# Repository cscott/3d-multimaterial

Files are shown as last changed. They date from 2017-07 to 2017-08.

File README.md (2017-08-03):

# Direct-drive multimaterial printing using Printrbot extruders

Thing tracker at
https://cscott.github.io/thing-tracker/#/thing/3367036c-9556-4aa5-b3d4-02ff7dc592d1

## Description

This repository contains a collection of parts used to implement
direct-drive multimaterial printing on a [Printrbot] Simple Metal.
It should be generalizable to other Printrbot models, and other
3d printers, but we generally use Printrbot extruder designs
and [Marlin]'s [Printrboard]/[Extrudrboard] support.  The basic
direct-drive multimaterial concept is due to [Brian Roe](http://roemotion.com)
([@MakerBrian](https://twitter.com/MakerBrian)).

The direct-drive design uses the standard extruder directly above the
hot end for precise no-lag filament control and compatibility with
flexible filaments.  It is wired up to the extruder output on the
[Printrboard] and controlled by Marlin as "Extruder 0".

We use a Printrbot [Gear Head Extruder] for direct drive, using the
fact that this extruder is self-loading: once filament is introduced
above the drive gears, the extruder will grab it and feed it through
without manual intervention.  (We're actually using the [beta version
of the gear head extruder](https://www.youmagine.com/designs/printrbot-gear-head-extruder) which used a printed housing.)

Above this direct-drive gear head extruder is a V-shaped merge adapter
which accepts 1-4 bowden tubes containing different filament
materials.  This is integrated with the housing of the gear head
extruder to place the merge as close to the extruder input as
possible.  This minimizes the distance that unsupported filament must
travel during filament changes, and thus (hopefully) prevents jams.

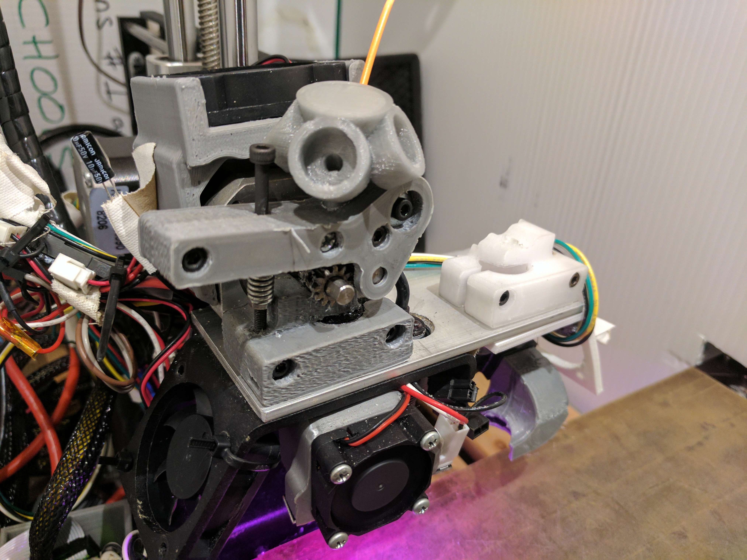
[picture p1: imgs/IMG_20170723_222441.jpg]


At the moment I've designed the merge as a single printed piece which
fits into an 8mm hole on direct-drive extruder handle or body.  The
idea is to make it easy to retrofit an existing gear-head extruder
by simply drilling an 8mm pocket in the handle, although I don't
own one of the newer Aluminum Gear Head Extruders to fully test this.

The bowden tubes from the merge piece run to individual bowden drives
mounted on filament spools.  I'm using SPANNERHANDS' excellent
[spool design](https://www.thingiverse.com/thing:2119644) with a
slight remix to move the PFTE coupler and mount an extruder where
the PFTE coupler used to attach.  The extruders connect to an
[Extrudrboard] or [Extrudrboard2] and feed the filament from the
spool into the bowden tube to direct it to the merge piece.
Two extruders are always driven simultaneously to move filament,
one on the spool and one at the print head, although during
filament change operations there may be times when no filament
is actually in contact with the direct drive, and thus the
spool extruders are working alone.

The [Marlin] firmware is modified to support this style of operation,
building on the `MK2_MULTIPLEXER` support upstreamed to support Prusa's
[Super Switch](https://github.com/prusa3d/Original-Prusa-i3/issues/29).

<br clear="both" />

## Instructions

### Step 1: Build spools

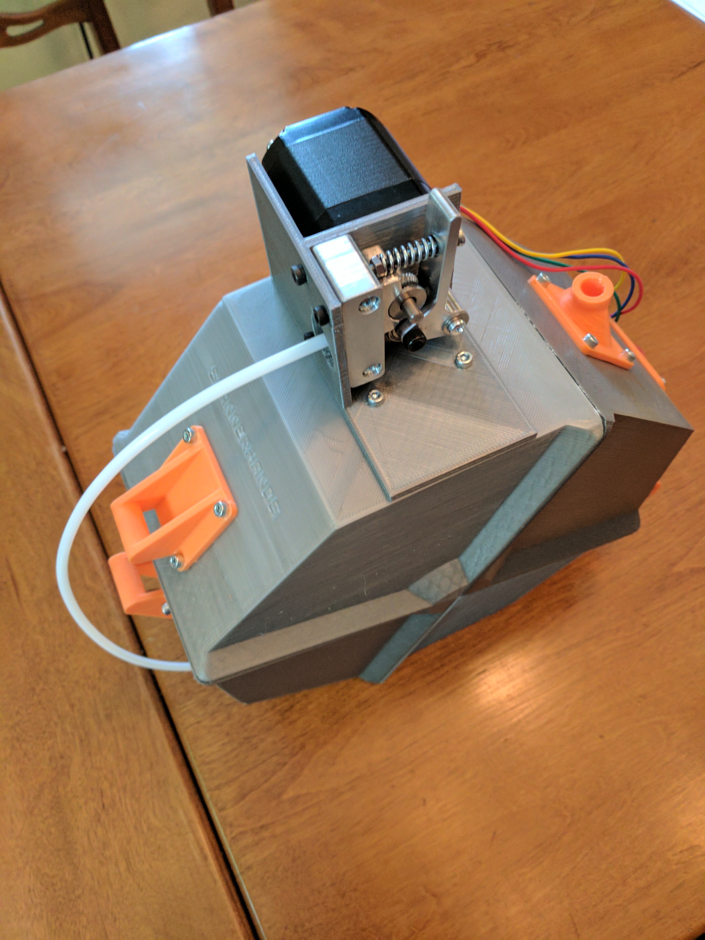
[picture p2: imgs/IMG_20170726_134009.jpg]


Start by printing out a [SPANNERHANDS spool] for each filament bowden
extruder you are going to use. I'm using the "v5 1kg" variant, but
with a little effort you could adapt these instructions to one of the
other spool variants.  Use [`spool-remix-lid2.stl`] instead of the
stock `LID2` part.  Mount the SPANNERHANDS `PTFE_COUPLER_v2_0.stl`
part to [`spool-remix-lid2.stl`].  We are going to mount our
bowden extruder on `LID1`, where the `PTFE_COUPLER` part would
normally go.  Assemble the `LID_Bracket`, `BASE_Bracket`,
and two `CLASP_BRACKET_v2_0` parts; I printed these in a contrasting
color.

Use two `Glue_Joint` parts to assemble the lid and base halves;
I recommend gluing both at once with the parts assembled into a complete
circle so you can ensure that the gap between top and bottom is not
too large as you glue them up.  Otherwise you tend to get top and bottom
halves which are ~178° of arc instead of 180°, and when you finally put
top and bottom together you get a pacman which won't close completely.
You can scale up the Z axis of the SPANNERHANDS `Flex_Seal` parts and
then trim them into a wedge to kludge around the problem if this happens.

I found the stock spool bearing mounts a little too tight, so I printed
the 50mm spool at 102% to fit my 52mm-core diameter spools with the right
fit for the bearings.  I use the remix at
[thing:2372633](https://www.thingiverse.com/thing:2372633) to fit my
32mm core diameter spools; I didn't need to scale that in any way.

<br clear="both" />

### Step 2: Mount bowden extruders

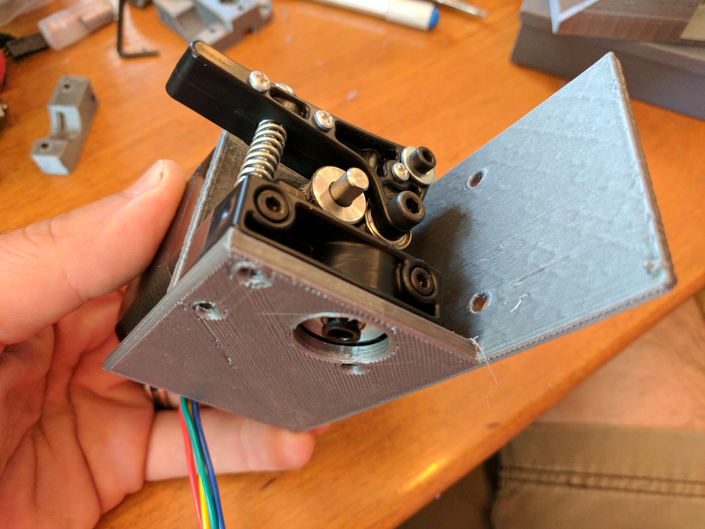
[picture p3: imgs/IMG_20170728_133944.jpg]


Now print out [`mount-1kg.stl`] and attach it to the LID1 part of the
spool, with four M3x10mm screws like all of the other SPANNERHANDS
spool parts.  After it is attached to the spool you can mount the
extruder, placing the mount between the extruder body and the stepper.
I recommend M3x25mm screws here; some models of Printrbot extruder
might need some extra length to account for the mounting plate between
the extruder and stepper.

You can optionally use three M3x8mm screws to secure the bottom of
the extruder.  Some models of Printrbot extruder (for example, the
injection-molded plastic extruder) don't have these mounting holes.
They are probably overkill for this use anyway.

<br clear="both" />
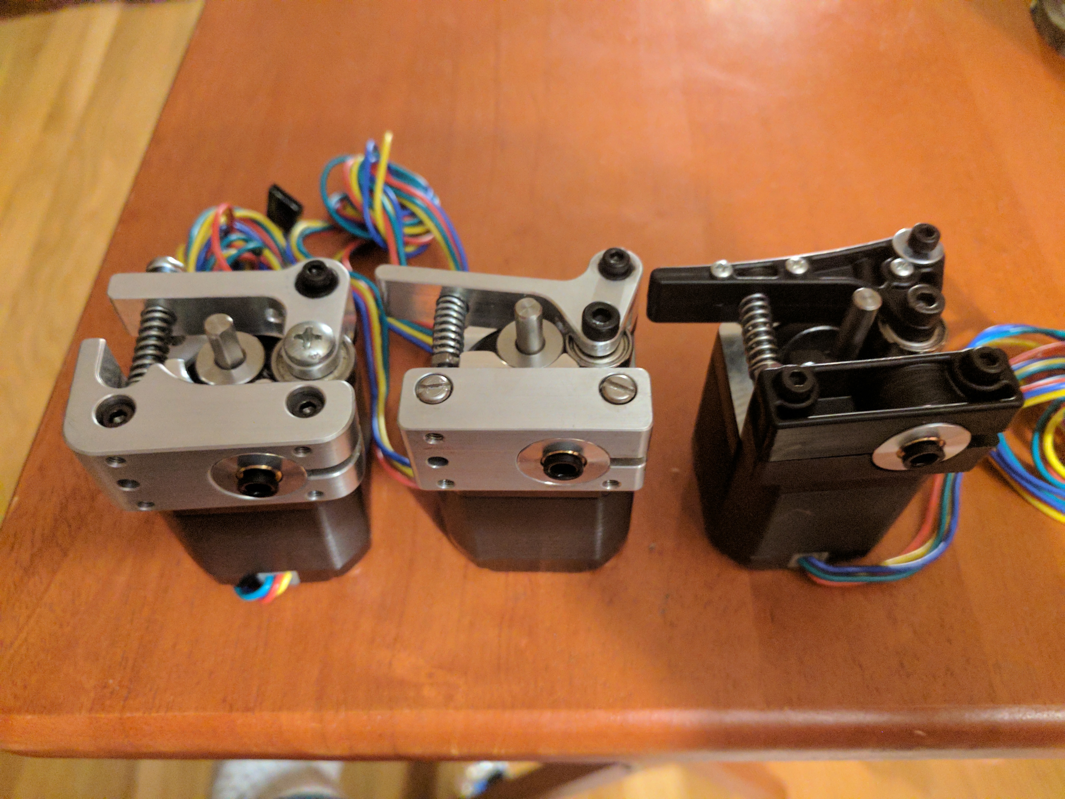
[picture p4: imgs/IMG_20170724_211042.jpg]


Insert a
[Groove mount 1.75mm Bowden coupler](https://www.filastruder.com/collections/e3d-spare-parts-and-accessories/products/bowden-couplings-all-types)
where the hotend would usually mount on the extruder.

<br clear="both" />
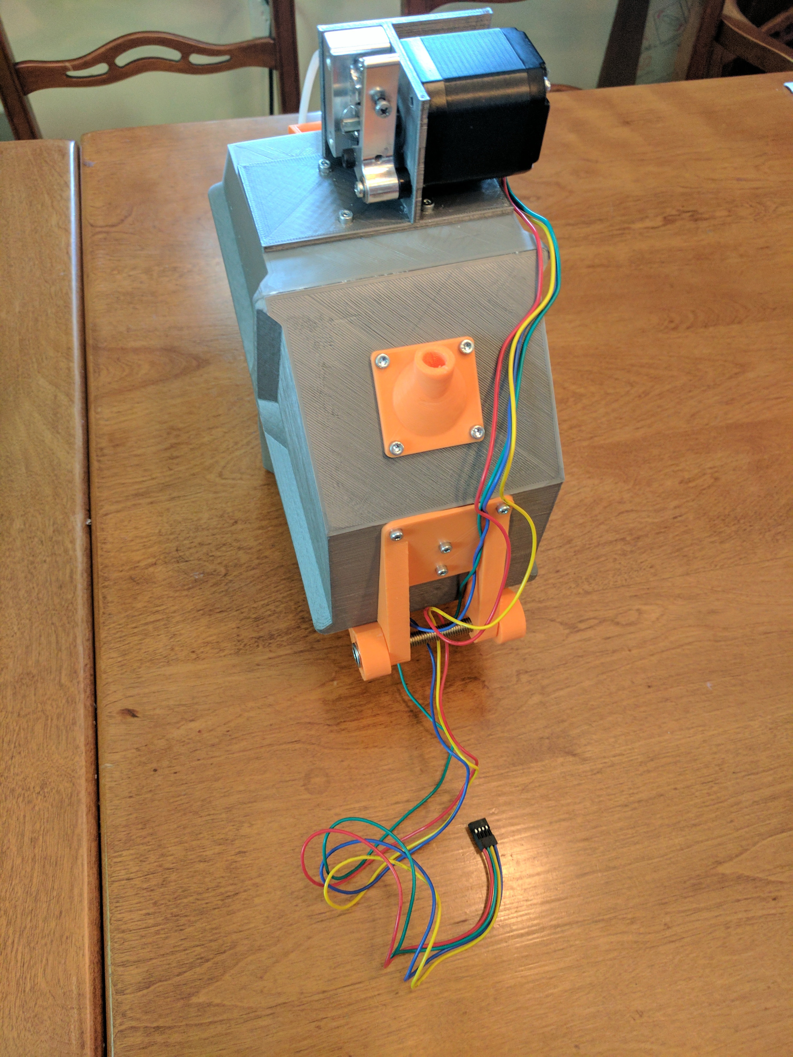
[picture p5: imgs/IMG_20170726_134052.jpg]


You can route the wires for the stepper down the back of the spool and
through the hinge.  You'll probably need [servo extension cables] to
reach your Extrudrboard/Extrudrboard2 from wherever you decide to
mount your spools.  You can use [`spool-remix-hanger.stl`] to mount
the spool to the wall while leaving room for the stepper motor cable.

<br clear="both" />

### Step 3: Assemble gear head direct-drive extruder

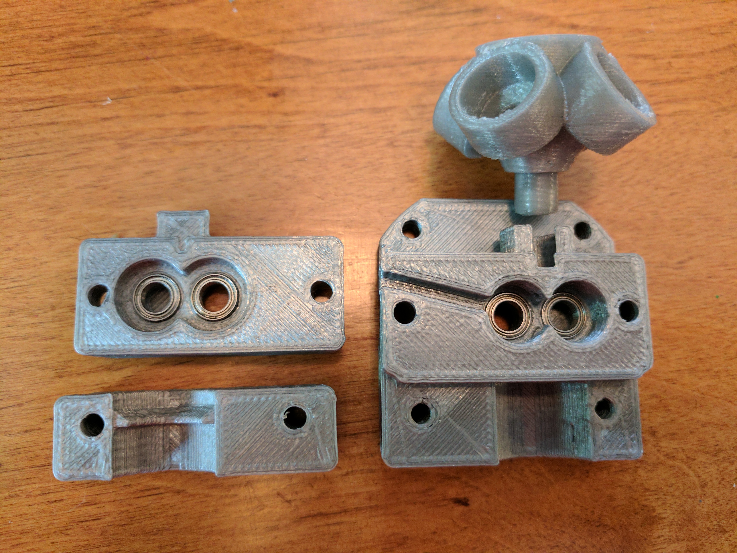
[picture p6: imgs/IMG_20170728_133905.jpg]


Print out [`gearhead-remix-base.stl`], [`gearhead-remix-clamp.stl`],
and [`gearhead-remix-gearbox.stl`]. (The photo also shows an early
version of [`bowden-block-4.stl`], the bowden merge piece.)

<br clear="both" />
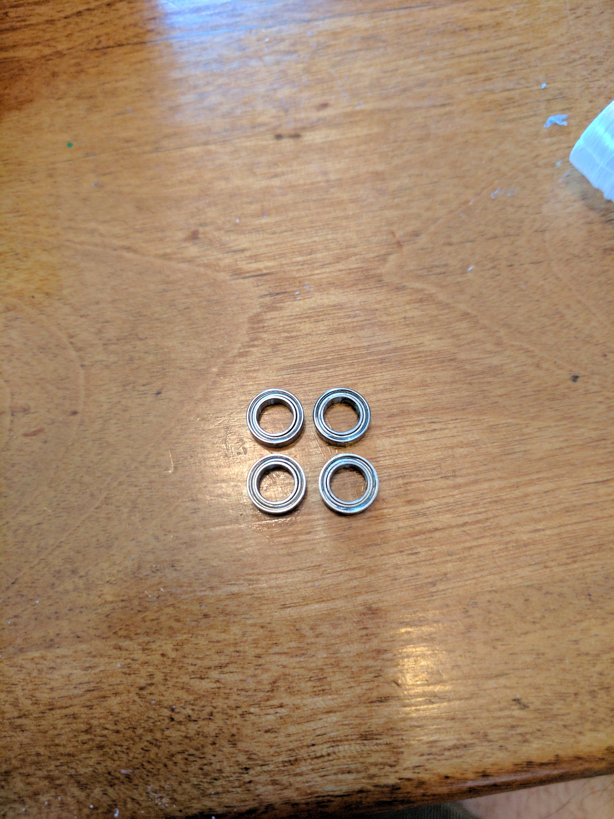
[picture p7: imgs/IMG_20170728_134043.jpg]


You'll also need (4) [5x8x2.5mm ball bearings] (or just three; see
note 2 below).

<br clear="both" />


First, install a pair of bearings into the `base` piece, and then install
the Printrbot Gear Head Extruder Gear Set into the bearings.

**NOTE 1:**
Printrbot [sells these](https://printrbot.com/shop/gear-head-extruder-gear-set/),
but the pair that I have came from the Beta program for the Gear Head Extruder.
It's possible the production gear set differs from the beta gears.

**NOTE 2:**
Printrbot's original instructions stated that the rear stepper motor
bearing (the bearing behind the hollow gear you just installed) is
optional.  But if you're buying bearings, no reason to pinch pennies.

**NOTE 3:**
You may want to try [walter](https://www.thingiverse.com/walter/about)'s
[remix of the gear head extruder](https://www.thingiverse.com/thing:1052966).
It appears to use the same Printrbot gear set and bearings---but again,
I'm not certain whether production gears differ from beta gears, and if so
which walter used.  Some modifications will be necessary to adapt his
remix to Printrbot bottom-mounting holes, but maybe you don't need those.

<br clear="both" />
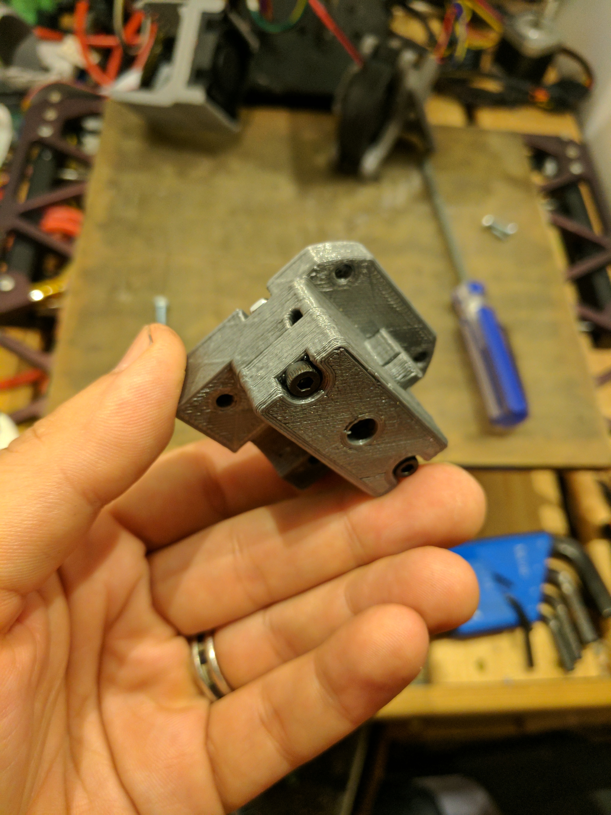
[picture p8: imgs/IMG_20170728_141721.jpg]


Now install the other pair of bearings into the `gearbox` piece, and
bolt it to the base using (2) M3x20mm screws and (2) M3 nuts, sandwiching
the gears between them.  Before closing things up, align the set screw in
the left-hand gear with the channel in the base; this will allow you to
insert an allen wrench to tighten this gear onto the stepper shaft.

<br clear="both" />
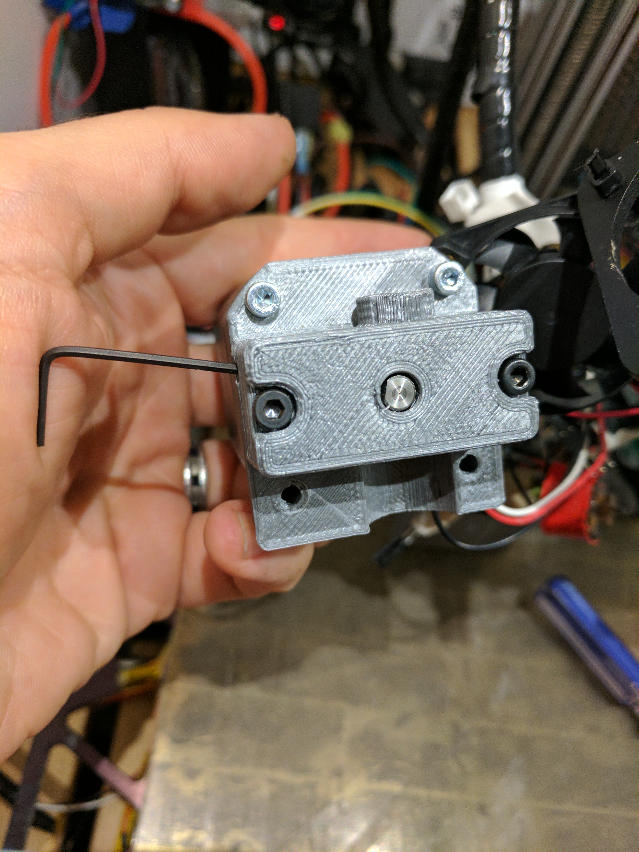
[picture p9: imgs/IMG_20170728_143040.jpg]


Attach the assembled gear box to the stepper.  Ensure the flat on the stepper
shaft is aligned with the allen wrench channel.  Use (2) M3x10mm screws in
the top holes to attach the gear box to the stepper, and then tighten the
set screw to secure the drive gear to the stepper shaft.

You probably want to use `M302 P1` to allow cold extrudes, then hook up
your stepper at this point and do a test extrusion w/o filament or hot end
in order to check that the gears turn smoothly without slipping or grinding.

<br clear="both" />
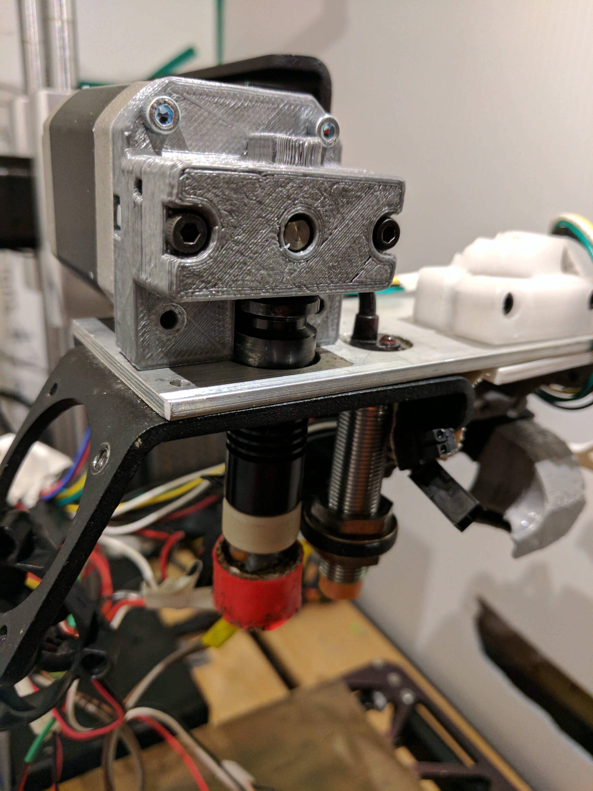
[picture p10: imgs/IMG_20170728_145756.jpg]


Now attach the extruder to the Y-axis of your printer using (2) M3x10mm
screws through the bottom mounting holes into (2) M3 nuts in the slots
provided.  (I'm using M3x12mm screws because I have an extra 3mm aluminum
plate mounted to my Y-axis, to support a previous dual-extruder
experiment [similar to this one](https://www.thingiverse.com/thing:1539380).)

Insert your hot end, and ensure it is snug and flush to the bottom surface
fof the extruder as shown in the picture.  Any gap here will allow flexible
coil to kink and coil into the gap, eventually pushing your hot end off in
the middle of a print.  (This is the voice of experience speaking.)

<br clear="both" />
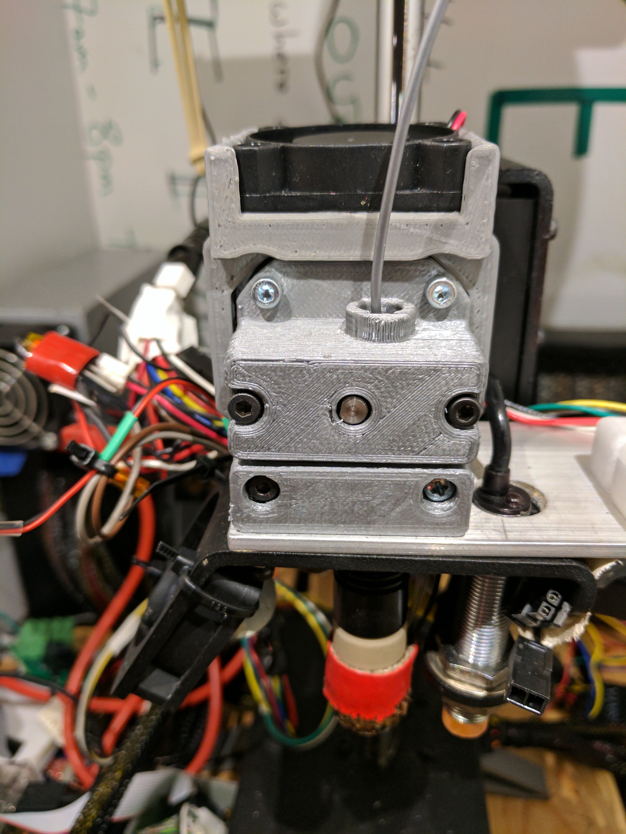
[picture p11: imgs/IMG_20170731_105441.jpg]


Install the `clamp` piece using two M3x22mm screws into the stepper.
There is a ridge on the clamp piece that should fit into the ring at
the top of your hot end and keep it from slipping downward.  Be
careful of the screw length here: if the screw is too long it will
bottom out in the blind mounting hole on the stepper and not bend the
PLA clamp piece enough to properly grip the hotend.  (Again, the voice
of experience.)  The `clamp` is secured to the Y-axis using another
M3x10mm screw and M3 nut into its bottom.

You can do a test print, feeding filament through the hole in
the top of the remixed gear head extruder, to make sure everything
is working correctly to this point.  Be sure to use `M92 E127` to
reset your extruder steps/mm if you weren't previously using a
gear head extruder.

<br clear="both" />

### Step 4: Install bowden merge piece

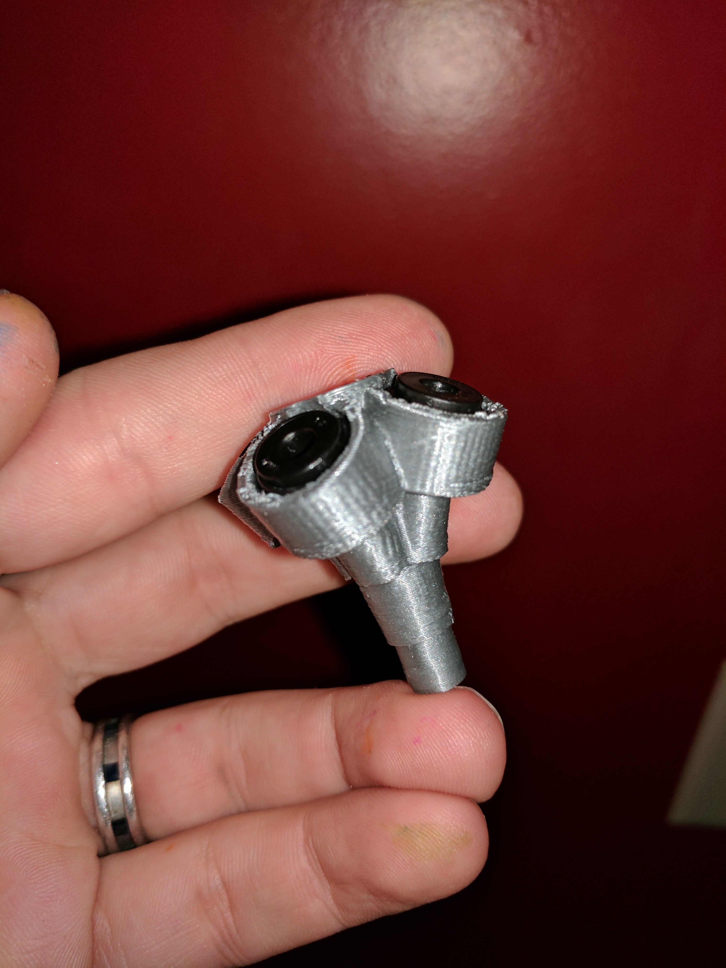
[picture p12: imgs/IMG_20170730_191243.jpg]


Print out [`bowden-block-4.stl`] and install (4)
[Filastruder/E3D "Embedded for plastic" 1.75mm Bowden Couplers](https://www.filastruder.com/collections/e3d-spare-parts-and-accessories/products/bowden-couplings-all-types).  (You could also use the 2-way or 3-way merge piece if
you prefer.)

To be continued...

<br clear="both" />

### Step 5: Wire up the bowden extruder steppers
### Step 6: Update Printrboard firmware
### Step 7: Test 'er out!

## Related

* The [Extrudrboard2] design allows connecting up to four multiplexed
  steppers to a Printrboard.
* [SPANNERHANDS spool] system.
* Printrbot [Gear Head Extruder].
* [Multimaterial community forum](http://forum.monstercafe.net/topic6.html)

## License

These designs are licensed under the [GPLv2+].

[Printrbot]: http://printrbot.com
[Printrboard]: http://reprap.org/wiki/Printrboard
[Extrudrboard]: http://reprap.org/wiki/Adding_more_extruders#RAMPS_using_ExtrudrBoard
[Extrudrboard2]: https://github.com/cscott/extrudrboard2
[Marlin]: http://www.marlinfw.org/
[Gear Head Extruder]: https://printrbot.com/shop/gear-head-extruder-v2/
[SPANNERHANDS spool]: https://www.thingiverse.com/thing:2119644
[servo extension cables]: http://www.ebay.com/itm/2-3-foot-XH2-54-Long-Stepper-Motor-Extension-Cables-for-3D-Printers-5-Pieces/272523242942
[5x8x2.5mm ball bearings]: https://amazon.com/gp/product/B00ZHST8NU/
[`spool-remix-lid2.stl`]: ./spool-remix-stl/spool-remix-lid2.stl
[`spool-remix-hanger.stl`]: ./spool-remix-stl/spool-remix-hanger.stl
[`mount-1kg.stl`]: ./mount-stl/mount-1kg.stl
[`gearhead-remix-base.stl`]: ./gearhead-remix-stl/gearhead-remix-base.stl
[`gearhead-remix-clamp.stl`]: ./gearhead-remix-stl/gearhead-remix-clamp.stl
[`gearhead-remix-gearbox.stl`]: ./gearhead-remix-stl/gearhead-remix-gearbox.stl
[`bowden-block-4.stl`]: ./bowden-stl/bowden-block-4.stl
[GPLv2+]: https://spdx.org/licenses/GPL-2.0+.html

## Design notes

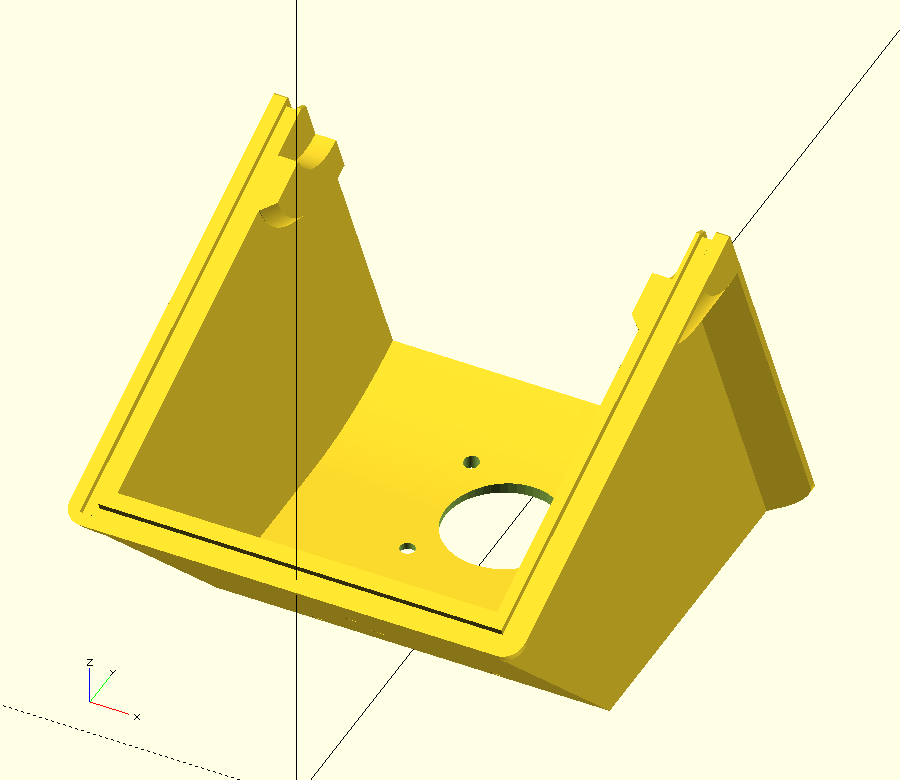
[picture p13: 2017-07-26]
thumbnails/spool-remix.png

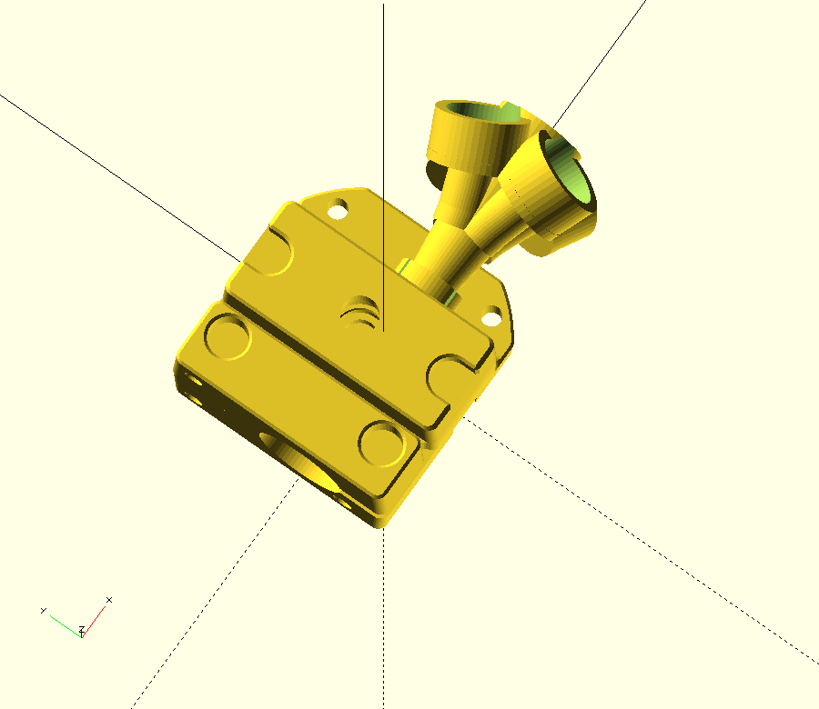
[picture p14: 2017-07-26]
thumbnails/gearhead-remix.png

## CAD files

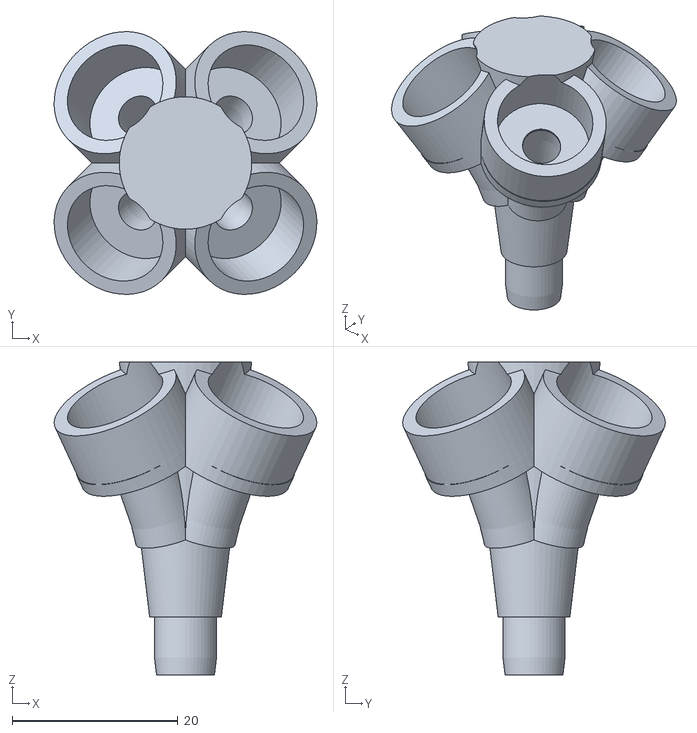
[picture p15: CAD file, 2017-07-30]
bowden-stl/bowden-block-4.stl
31.7 x 31.7 x 37.8

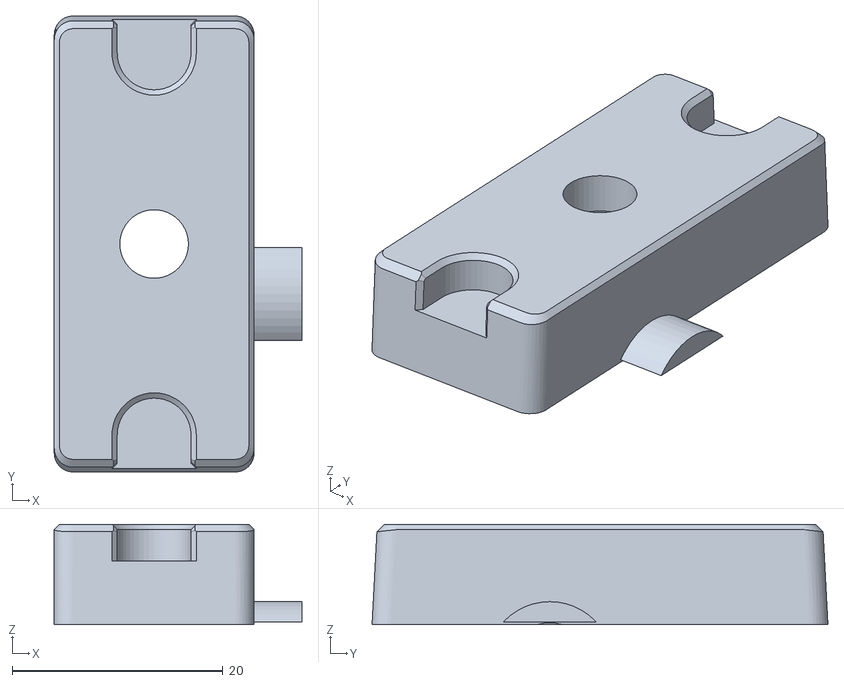
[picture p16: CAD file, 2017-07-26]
gearhead-remix-stl/gearhead-remix-gearbox.stl
23.5 x 43.2 x 9.52

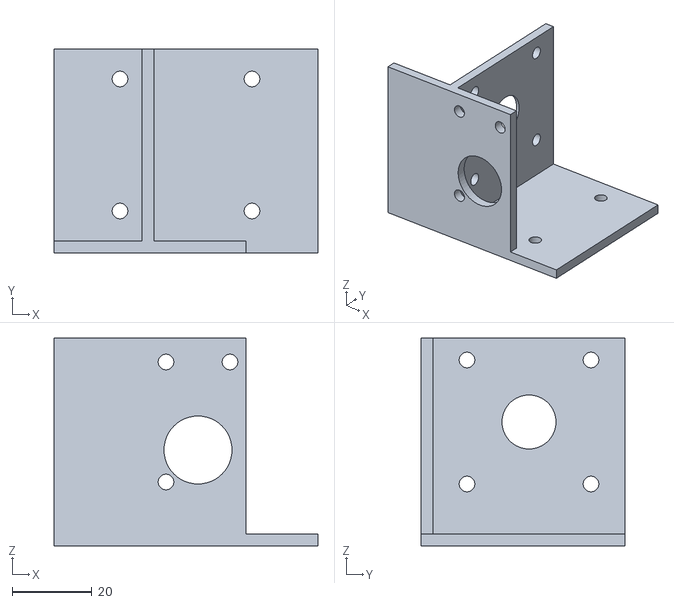
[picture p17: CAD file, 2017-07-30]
mount-stl/mount-750g.stl
66.0 x 51.0 x 52.0

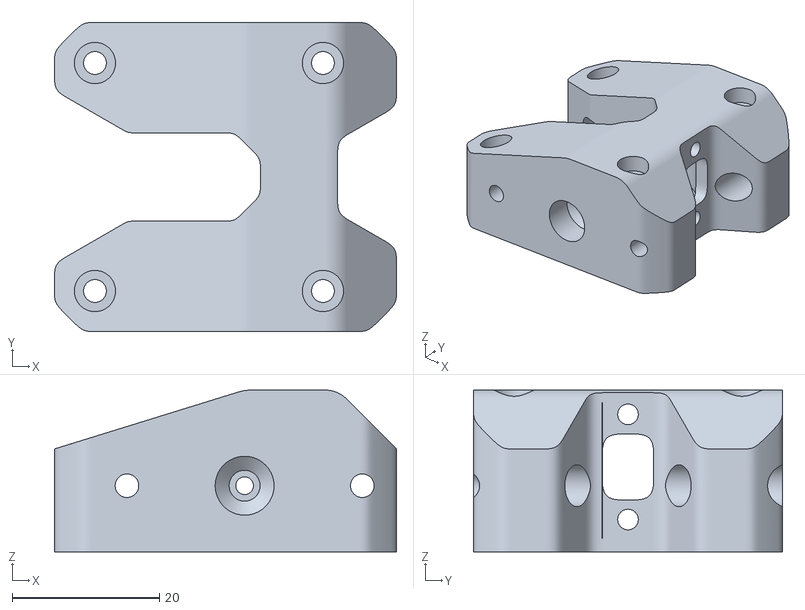
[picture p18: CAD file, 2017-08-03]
remix/Gearhead_v6-1.STL
46.5 x 42.0 x 22.0

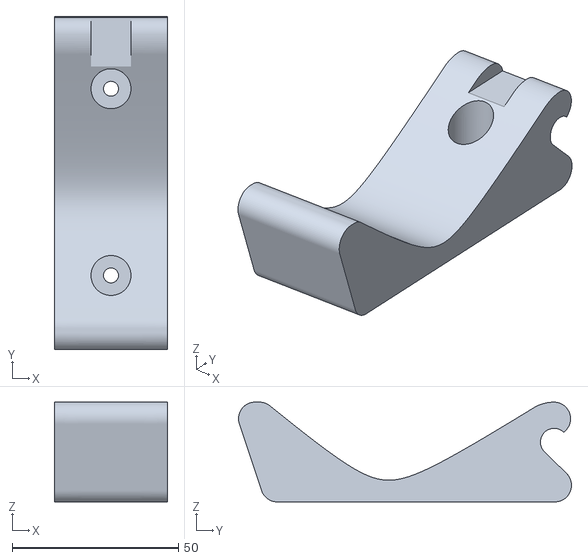
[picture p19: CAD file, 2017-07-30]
spool-remix-stl/spool-remix-hanger.stl
34.0 x 100.1 x 30.0

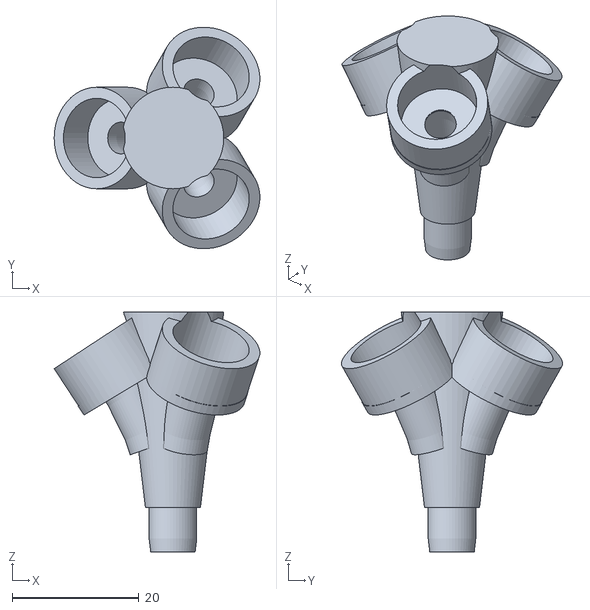
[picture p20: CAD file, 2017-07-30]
bowden-stl/bowden-block-3.stl
32.4 x 34.9 x 37.8

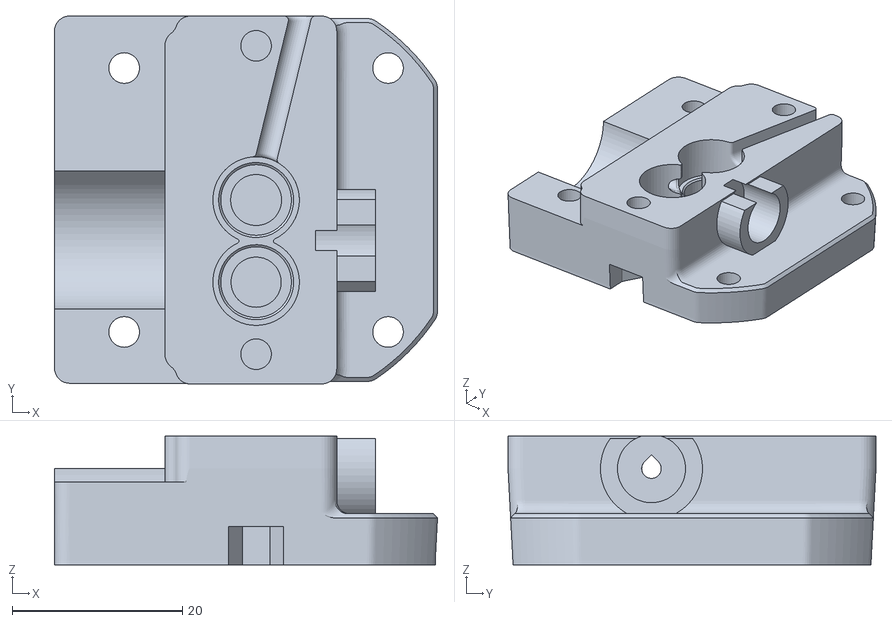
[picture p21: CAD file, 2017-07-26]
gearhead-remix-stl/gearhead-remix-base.stl
45.0 x 43.2 x 15.1

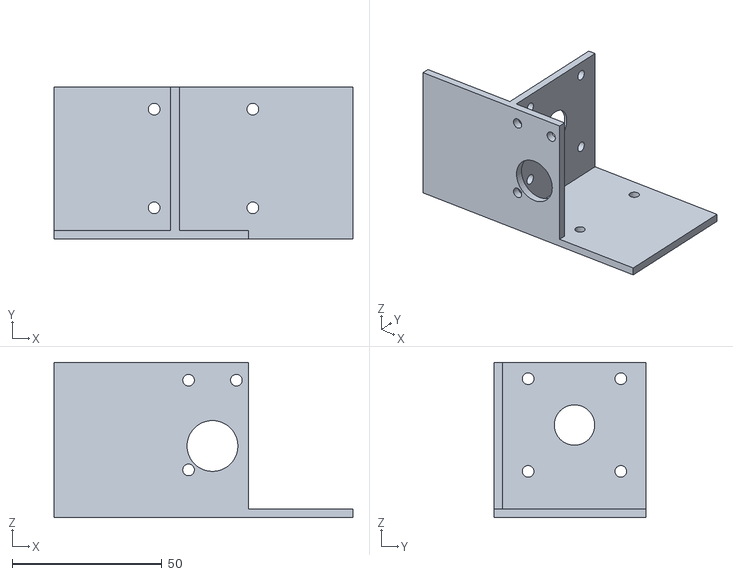
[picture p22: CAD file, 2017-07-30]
mount-stl/mount-1kg.stl
100.0 x 51.0 x 52.0

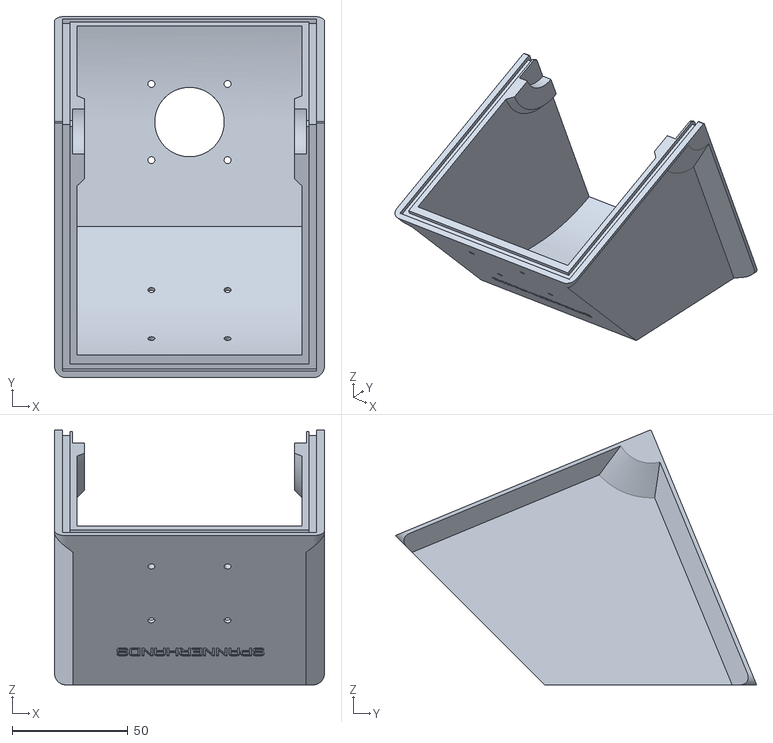
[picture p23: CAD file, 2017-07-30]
remix/v5_Small_Volume_1kg_LID_1.stl
116.7 x 156.2 x 110.1

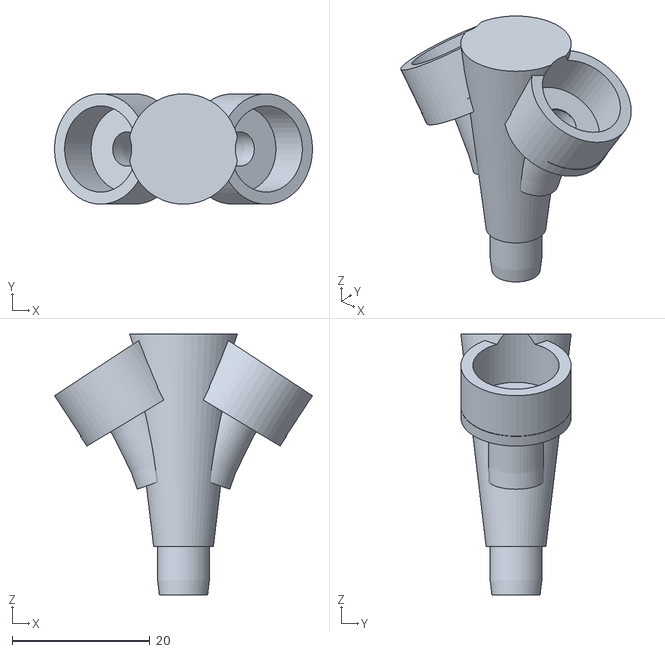
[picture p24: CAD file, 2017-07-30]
bowden-stl/bowden-block-2.stl
37.4 x 16.0 x 37.8

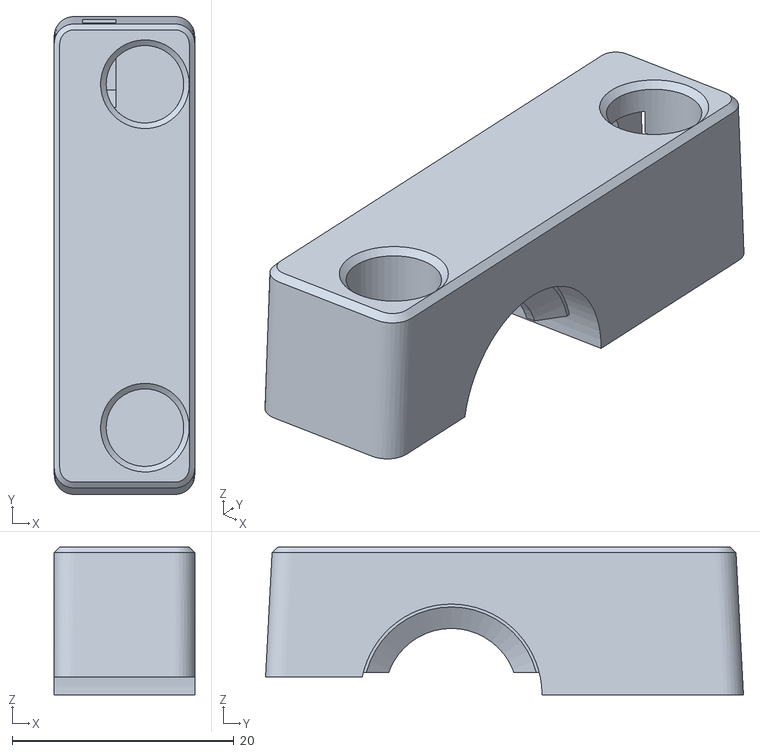
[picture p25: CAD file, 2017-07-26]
gearhead-remix-stl/gearhead-remix-clamp.stl
12.7 x 43.1 x 13.3

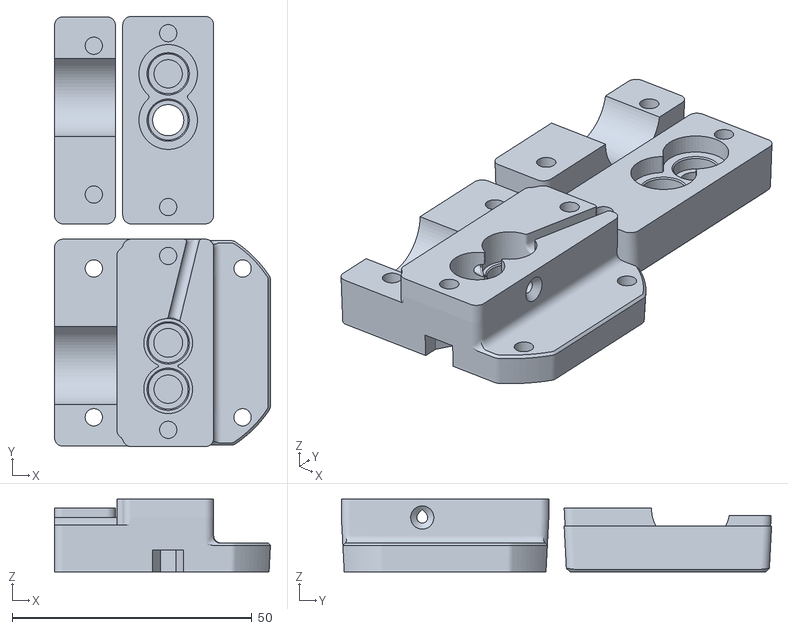
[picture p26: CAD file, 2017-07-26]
remix/Printrbot_Gear_Head_v0.02.1.stl
45.0 x 89.6 x 15.1

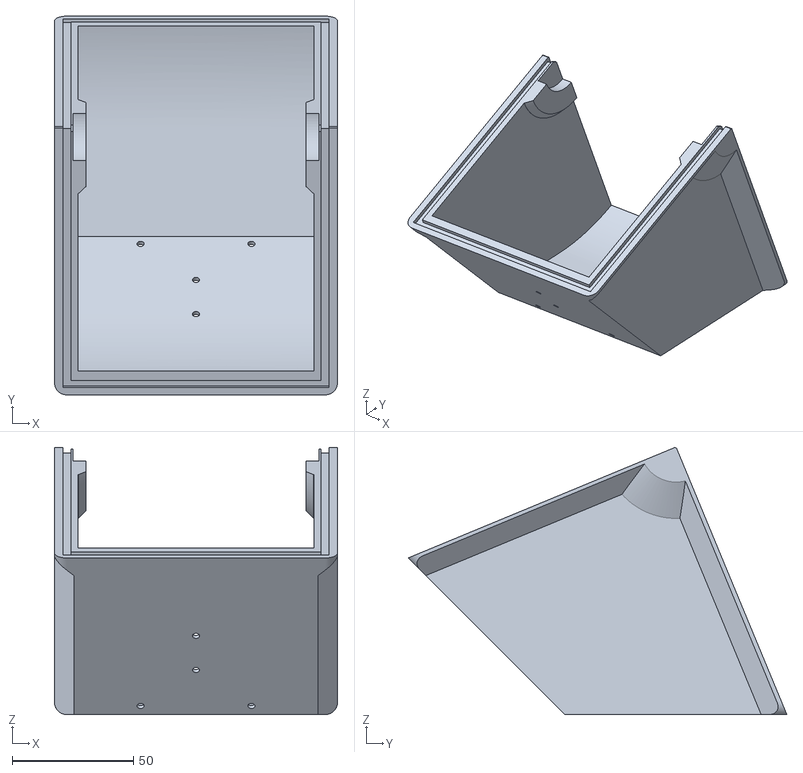
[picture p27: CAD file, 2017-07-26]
remix/v5_Small_Volume_1kg_LID_2.stl
116.7 x 156.2 x 110.1

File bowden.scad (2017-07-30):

/* Adapter from 2-4 bowden tubes to input of Printrbot Gear Head Extruder. */

/* [Global] */

// Which part.
part = "block"; // [block]

// How many inputs
ntubes = 4; // [2,3,4]

/* [Hidden] */

// PFTE bowden tube
function tube_diam() = 4;
function core_diam() = 2;
function tube_extra_diam() = 0.5; // clearance for tube
function core_extra_diam() = 0.5; // clearance for filament
// plastic mount from filastruder
function mount_diam() = 12;
function mount_deep() = 7;
// interface to gear head extruder
function handle_diam() = 7.5; // for 8mm drill
function handle_deep() = 7;

// amount to enlarge diameter of holes to account for filament spread
function inner_clearance() = 0.5;
draft=false;
$fn = draft ? 12 : 48;

if (part=="block") {
  block("all");
} else if (part=="straight_bowden") {
  straight_bowden();
} else if (part=="straight_cluster") {
  straight_cluster();
} else if (part=="curved_bowden") {
  curved_bowden();
} else if (part=="curved_cluster") {
  curved_cluster();
}

module block(part="all", ntubes=ntubes) {
  // less sharp, fits on gearhead extruder v0.02 better
  curve_radius = 50;
  length = 36;
  block_cutoff = 19;
  cone_height = 37.8;
  cone_diam = 16;
  extra_len = 10;
  /*
  // most compact:
  block_cutoff = 10.5;
  curve_radius = 20;
  cone_height = 27.4;
  cone_diam = 20;
  length = 26;
  extra_len = 10;
  */

  if (part=="all") {
    difference() {
      block(part="outside");
      block(part="hole");
      difference() {
        cube([cone_diam,cone_diam,2*handle_deep()], center=true);
        cylinder(d=handle_diam(), h=3*handle_deep(), center=true);
      }
    }
  } else if (part=="outside") {
    wall=2;
    union() {
      // aids printability by giving flat face on bottom
      translate([0,0,cone_height]) scale([1,1,-1])
        cylinder(d1=cone_diam,
                 d2=handle_diam()-0.5,
                 //was: d2=core_diam() + core_extra_diam() + 2*wall,
                 h=cone_height);
      curved_cluster(part="core", ntubes=ntubes,
                curve_radius=curve_radius, length=length,
                extra_diam=mount_diam() - core_diam() + 2*wall,
                cutoff_length=length - mount_deep() - wall);
      curved_cluster(part="tube", ntubes=ntubes,
                curve_radius=curve_radius, length=length,
                extra_diam=2*wall, cutoff_length = block_cutoff - wall);
    }
  } else if (part=="hole") {
    curved_cluster(part="core", ntubes=ntubes,
                   curve_radius=curve_radius, length=length,
                   extra_len=1,
                   extra_diam=core_extra_diam() + inner_clearance());
    curved_cluster(part="hole", ntubes=ntubes,
                   curve_radius=curve_radius, length=length,
                   extra_len=extra_len, extra_diam=inner_clearance());
    curved_cluster(part="tube", ntubes=ntubes,
                   curve_radius=curve_radius, length=length,
                   cutoff_length=block_cutoff,
                   extra_diam=tube_extra_diam() + inner_clearance());
  }
}

module straight_cluster(part="all", ntubes=ntubes, angle=25, length=28) {
  rotate([0,0,ntubes==4 ? 45: 0])
  for(i=[1:(draft?1:ntubes)]) rotate([0,0,i*(360/ntubes)]) {
    rotate([angle, 0, 0]) straight_bowden(part=part, length=length);
  }
}

module curved_cluster(part="all", ntubes=ntubes, curve_radius=50, length=36, cutoff_length=0, extra_len=0, extra_diam=0) {
  rotate([0,0,ntubes==4 ? 45: 0])
  for(i=[1:(draft?1:ntubes)]) rotate([0,0,i*(360/ntubes)]) {
    curved_bowden(part=part, length=length, curve_radius=curve_radius,
                  cutoff_length=cutoff_length,
                  extra_len=extra_len, extra_diam=extra_diam);
  }
}

module curved_bowden(part="all", length=28, curve_radius=20, cutoff_length=0, extra_len=0, extra_diam=0) {
  epsilon = .1;
  // compute curve_angle from length (2*pi*r / 360)
  curve_angle = (length - mount_deep()) * 360 / (2*PI*curve_radius);
  cutoff_angle = (cutoff_length > 0 ? cutoff_length : -extra_len) * 360 / (2*PI*curve_radius);

  if (part=="all") {
    curved_bowden(part="cap", length=length, curve_radius=curve_radius);
    difference() {
      curved_bowden(part="tube", length=length, curve_radius=curve_radius);
      curved_bowden(part="core", length=length, curve_radius=curve_radius, extra_len=epsilon);
    }
  } else if (part=="tube" || part=="core") {
    diam = ((part=="tube") ? tube_diam() : core_diam()) + extra_diam;
    translate([-curve_radius,0,0]) rotate([90,0,0]) intersection() {
      rotate_extrude(convexity=10)
        translate([curve_radius, 0, 0])
          circle(d=diam);
      linear_extrude(height = 2*diam, center=true, convexity=10)
        polygon(points=[
          [0, 0],
          [curve_radius+diam, tan(cutoff_angle)*(curve_radius+diam)],
          [curve_radius+diam, tan(curve_angle)*(curve_radius+diam)]
        ]);
    }
    translate([-curve_radius,0,0]) rotate([0,-curve_angle,0])
      translate([curve_radius,0,-epsilon])
        cylinder(d=diam, h=mount_deep() + epsilon + extra_len);
  } else if (part=="hole") {
    translate([-curve_radius,0,0]) rotate([0,-curve_angle,0])
      translate([curve_radius,0,0])
        cylinder(d=mount_diam() + extra_diam, h=mount_deep() + extra_len);
  } else if (part=="cap") {
    difference() {
      curved_bowden(part="hole", length=length, curve_radius=curve_radius);
      curved_bowden(part="tube", length=length, curve_radius=curve_radius,
                    extra_len=epsilon, extra_diam=inner_clearance());
    }
  }
}

module straight_bowden(part="all", length=30, cutoff_length=0, extra_len=0, extra_diam=0) {
  cutoff = (cutoff_length > 0 ? cutoff_length : -extra_len);
  epsilon = .1;

  if (part=="all") {
    straight_bowden(part="cap", length=length);
    difference() {
      straight_bowden(part="tube", length=length);
      straight_bowden(part="core", length=length, extra_len=epsilon);
    }
  } else if (part=="tube" || part=="core") {
   diam = ((part=="tube") ? tube_diam() : core_diam()) + extra_diam;
   translate([0,0,cutoff])
   cylinder(d=diam, h=length + extra_len - cutoff);
  } else if (part=="hole") {
    translate([0,0,length - mount_deep()])
      cylinder(d=mount_diam() + extra_diam, h=mount_deep() + extra_len);
  } else if (part=="cap") {
    difference() {
      straight_bowden(part="hole", length=length);
      straight_bowden(part="tube", length=length,
                      extra_len=epsilon, extra_diam=inner_clearance());
    }
  }
}

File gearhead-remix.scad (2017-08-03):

/**
 * Remix of "Printrbot_Gear_Head_v0.02.1.stl" from
 * https://www.youmagine.com/designs/printrbot-gear-head-extruder
 * to add hotend capture ridge and mount for N-way bowden coupler.
 */

/* [Global] */

part = "all"; // [base, clamp, gearbox]

/* [Hidden] */

use <./mount.scad>
use <./bowden.scad>
$fn=48;

function bowden_coupler_off() = [7,0,11.3];
function bowden_coupler_len() = 7;

if (part=="walter") {
  walter_gearhead_remix();
  if (false) { // visualization for checking bearing size only
    translate([5,0,7.1])
      walter_bearing();
    translate([5,0,-4.5])
      walter_bearing();
  }
} else {
  gearhead_remix(part=part);
  if (part=="all") {
    translate(bowden_coupler_off()) rotate([0,90,0])
      block(part="all", ntubes=3);
  }
}

module gearhead() {
  // From: https://www.youmagine.com/designs/printrbot-gear-head-extruder
  translate([0,4.76,-2.56])
  import("remix/Printrbot_Gear_Head_v0.02.1.stl", convexity=10);
}

module walter_gearhead() {
  // From: https://www.thingiverse.com/thing:1052966
  // Move filament path to y axis and gear centers to x axis
  translate([-26.645,-21.325,-9.03])
  import("remix/Gearhead_v6-1.STL", convexity=10);
}

// ** Remix of Printrbot Gear Head extruder design **

module gearhead_bounds(part="base") {
  if (part=="base") {
    cube([50,55,30.3], center=true);
  } else if (part=="clamp") {
    translate([-18,52,0])
      cube([16,49,26.8], center=true);
  } else if (part=="gearbox") {
    translate([0,52,0])
      cube([20,49,19.2], center=true);
  } else if (part=="clamp-split") {
    translate([-20.73,0,11.3])
    cube([20,65,4], center=true);
  } else if (part=="gear-split") {
    translate([9.3,0,15.1])
    cube([40,65,0.5], center=true);
  }
}

module gearhead_part(part, just_bounds=false) {
  if (just_bounds) {
    gearhead_bounds(part=part);
  } else {
    intersection() {
      gearhead();
      gearhead_bounds(part=part);
    }
  }
}

module gearhead_assembled(part, just_bounds=false) {
  if (part=="all") {
    gearhead_assembled("base", just_bounds);
    gearhead_assembled("clamp", just_bounds);
    gearhead_assembled("gearbox", just_bounds);
  } else if (part=="base") {
    gearhead_part(part, just_bounds);
  } else if (part=="clamp" || part=="gearbox") {
    translate([0,55.925,24.64])
      rotate([180,0,0])
      gearhead_part(part, just_bounds);
  }
}

module gearhead_remix(part="all") {
  extruder_stop_off = [-10.71,0,bowden_coupler_off().z];
  intersection() {
    union() {
      difference() {
        union() {
          gearhead_assembled(part);
          difference() {
            translate(bowden_coupler_off()) rotate([0,90,0])
              ring(outer=12, inner=7, height=bowden_coupler_len());
            gearhead_bounds("gear-split");
          }
        }
        // bowden coupler mount
        translate(bowden_coupler_off()) // original guide is d=2.3 here
          rotate([0,90,0])
            cylinder(d=8, h=bowden_coupler_len() + 1);
      }
      // add extruder stop
      epsilon = .05;
      if (part=="clamp") difference() {
        translate(extruder_stop_off) rotate([0,-90,0]) difference() {
          translate([0,0,3 + epsilon])
            cylinder(d=18, h=1.5+.75 - epsilon);
          cylinder(d=12, h=6);
          translate([0,0,3])
            cylinder(d1=16, d2=12, h=1.5);
        }
        gearhead_bounds("clamp-split");
      }
    }
    union() {
      gearhead_assembled(part, just_bounds=true);
      if (part=="all" || part=="gearbox") {
        translate([bowden_coupler_len(),0,0]) gearhead_assembled(part, just_bounds=true);
      }
    }
  }
}

// ** Remix of Printrbot Gear Head extruder design **

module walter_gearhead_remix() {
  walter_gearhead();
  // TO DO:
  // 1. Add mount for bowden merge piece.
  // 2. Add hotend mount, w/ set screw through groove to secure?
  // 3. Add printrbot-standard mounting holes on bottom; trim bottom
  // to correct height; fill in existing mounting holes
  // 4. Add ring around bearing printed in flexible filament so that
  // "tension adjustment" setscrew affects force not position?
}

module walter_bearing() {
  ring(outer=8, inner=5, height=2.5); // 5x8x2.5mm, like on original kit
}


// ** Utilities **

module ring(outer, inner, height, center=false) {
  epsilon=.1;
  translate([0,0,center?(-height/2):0]) difference() {
    cylinder(d=outer, h=height);
    translate([0,0,-epsilon])
      cylinder(d=inner, h=height + 2*epsilon);
  }
}

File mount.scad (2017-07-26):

/*
 * Extruder mount onto SPANNERHANDS Filament Spools
 * https://www.thingiverse.com/thing:2119644
 */

/* [Global] */

size = "1kg"; // [750g, 1kg]
with_nema_plate = true; // [false,true]

/* [Hidden] */

mount_width = (size=="1kg") ? 100 : 66;
// 3 pieces, which we call A, B, and C.
a_thick = 3;
b_thick = 3;
c_thick = with_nema_plate ? 3 : 0;
// offset extruder from center in order to clear screws
stepper_offset = 3;
$fn=48;

function inch() = 25.4;
// hole diameter for an M3 screw
function m3_clear() = 3.4;
// amount to enlarge diameter of holes to account for filament spread
function inner_clearance() = 0.5;

module mount() {
  spannerhands_spacing = 33;
  hotend_height = 21; // hotend spacing above top of A
  hotend_diam = 16 + 0.5/*clearance*/;
  hotend_setback_width = 12;
  hotend_to_wall_width = 22 - 11;
  stepper_shaft_diam = 5 + 8/*clearance for hobbed wheel*/;
  stepper_ring_diam = 22;
  stepper_ring_depth = 2;
  nema17_mount = 31;
  extruder_mount_height = 30; // spacing between extruder mounting holes
  extruder_mount_width = 16; // spacing between extruder mounting holes

  a_width = mount_width;
  a_depth = 48 + b_thick;
  a_height = a_thick;

  b_width = a_width/2 + stepper_offset + hotend_setback_width;
  b_depth = b_thick;
  b_height = a_thick + hotend_height + 28;

  c_width = c_thick;
  c_depth = a_depth;
  c_height = b_height;

  // part a
  if (a_thick > 0) difference() {
    translate([-a_width/2, -(a_depth - 24), 0])
      cube([a_width, a_depth, a_height]);
    for (i=[-1,1]) for (j=[-1,1]) scale([i,j,1])
      translate([spannerhands_spacing/2,spannerhands_spacing/2,0])
        m3_hole();
  }
  // part b
  if (b_thick > 0) difference() {
    translate([-a_width/2, -(a_depth - 24), 0])
      cube([b_width, b_depth, b_height]);
    translate([stepper_offset, -(a_depth - 24), a_thick + hotend_height]) {
      rotate([90,0,0])
        cylinder(d=hotend_diam + inner_clearance(), h=3*b_thick, center=true);
      translate([0,0,-8]) {
        for (i=[-1,1]) scale([i,1,1]) {
          translate([-extruder_mount_width/2,0,extruder_mount_height])
            rotate([90,0,0]) m3_hole();
        }
        translate([-extruder_mount_width/2,0,0])
          rotate([90,0,0]) m3_hole();
      }
    }
  }
  // part c
  if (c_thick > 0) difference() {
    translate([stepper_offset - hotend_to_wall_width - c_thick,
               -(a_depth - 24), 0])
      cube([c_width, c_depth, c_height]);
    translate([stepper_offset - hotend_to_wall_width - c_thick,
               0,
               a_thick + hotend_height - 8 + extruder_mount_height/2]) {
      rotate([0,90,0]) {
        cylinder(d=stepper_shaft_diam + inner_clearance(), h=3*c_thick, center=true);
        cylinder(d=stepper_ring_diam + inner_clearance(), h=2*stepper_ring_depth, center=true);
      }
      for (i=[-1,1]) for (j=[-1,1]) scale([1,i,j])
        translate([0,nema17_mount/2,nema17_mount/2])
          rotate([0,90,0]) m3_hole();
    }
  }
}

module m3_hole(h=10, center=true) {
  cylinder(d=m3_clear() + inner_clearance(), h=h, center=center);
}

mount();

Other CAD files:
spool-remix-stl/spool-remix-lid2.stl
remix/WALL_MOUNT_v2_0.stl
spool-remix.scad

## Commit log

2017-07-20 first draft of multimaterial bowden head.
    [bowden.scad]
2017-07-22 Trim bottom to fit neatly into an 8mm hole in extruder handle.
    [bowden.scad]
2017-07-23 Use standard render script.
    [bowden.scad]
2017-07-23 Correct for inner clearance.
    [bowden.scad]
2017-07-23 Clean up; allow for 2, 3, or 4 tube inputs.
    [bowden.scad]
2017-07-25 Begin to add thing-tracker metadata.
    [bowden-block-2.stl, bowden-block-3.stl, bowden-block-4.stl]
2017-07-26 First version of bowden extruder mount for spool (thing:2119644).
    [mount-1kg.stl, mount-750g.stl, mount.scad]
2017-07-26 Extruder mount v2: fixed spannerhands mount spacing, more stepper clearance.
    [mount-1kg.stl, mount-750g.stl, mount.scad]
2017-07-26 Add remix of SPANNERHANDS lid2 to add new PFTE coupling mount.
    [spool-remix-lid2.stl, spool-remix.scad, v5_Small_Volume_1kg_LID_2.stl]
2017-07-26 Add remix of Printrbot Gear Head v0.02 to accomodate bowden merge.
    [Printrbot_Gear_Head_v0.02.1.stl, bowden-block-2.stl, bowden-block-3.stl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]
2017-07-30 Tweak bowden tube cutoff in merge piece.
    [bowden-block-2.stl, bowden-block-3.stl, bowden-block-4.stl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]
2017-07-30 Regenerate mount stls from scad sources.
    [mount-1kg.stl, mount-750g.stl]
2017-07-30 Add a remixed version of the spool wall hanger.
    Notch the wall hanger to allow the stepper motor wires to pass
    through neatly.
    [WALL_MOUNT_v2_0.stl, spool-remix-hanger.stl, spool-remix.scad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]
2017-07-31 Forgot to describe attaching the clamp piece to the extruder.
2017-07-31 Photo of assembled gear head extruder; M3 screw copy edits.
2017-08-03 Add Walter's version of Gear Head extruder, thing:1052966
    Walter's extruder from: https://www.thingiverse.com/thing:1052966
    Add some notes to the README describing this option. You'd need to
    make some tweaks to make it work with Printrbot bottom-mounting
    screws, but some Printrbot models don't use those.
    [Gearhead_v6-1.STL, gearhead-remix.scad]
2017-08-03 Notes about clamp screw length.
